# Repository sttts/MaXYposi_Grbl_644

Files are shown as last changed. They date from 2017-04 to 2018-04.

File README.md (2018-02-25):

GitHub Logo

Maker Media GmbH und c't, Heise Zeitschriften Verlag

***

### MaXYposi-Schrittmotorsteuerung 

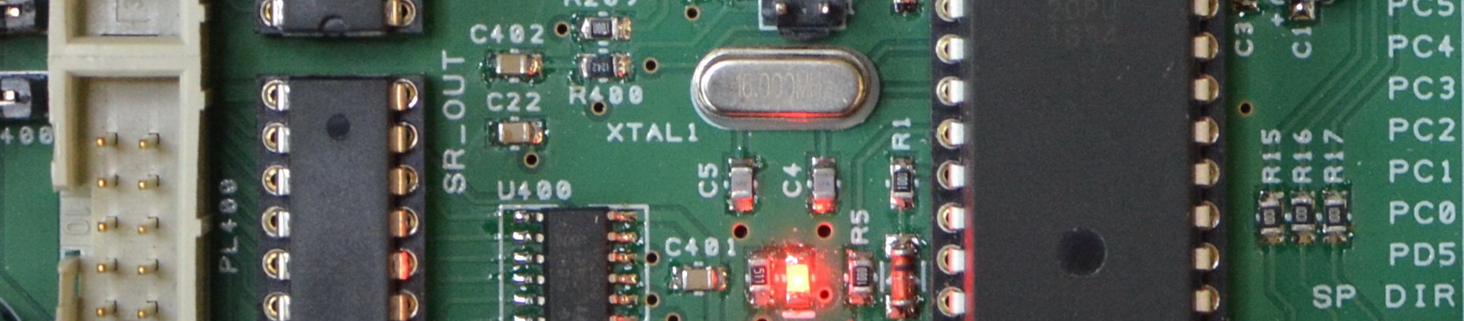
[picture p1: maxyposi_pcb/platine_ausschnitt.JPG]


Unser auf GRBL basierendes CNC-Steuerungs-Projekt für **4 Achsen und vielen 
I/Os** auf einer speziell für CNC-Zwecke ausgelegten Platine. Natürlich wäre als 
Bahnsteuerung auch ein normaler Arduino-328 mit dem Standard-GRBL geeignet - wir 
haben unser GRBL-644 allerdings auf 4 Achsen erweitert und 32 I/Os hinzugefügt, 
außerdem einen Handrad- und Joystick-Jog-Anschluss sowie eine Echtzeit-
Positionsanzeige mit LCD 16x2 auf einem (optionalen) Bedienfeld. 

Die mit allen SMD-Bauteilen vorbestückte Platine wird mit einem programmierten 
ATmega644A (Optiboot-Bootloader und GRBL 1.1f4 ohne Kontrollpult-Unterstützung) geliefert und kann 
im [Heise Shop](https://shop.heise.de/sonstiges/make-projekte/maxyposi) bestellt werden. Weitere Hinweise
finden Sie auf der [MaXYPosi-Projektseite](http://www.make-magazin.de/maxyposi). 

**Wichtig:** Für den Einsatz des MaXYpulti-Kontrollpults müssen Sie den Arduino-Sketch neu kompilieren und hochladen 
(Hinweise dazu im Unterverzeichnis **[MaXYpulti PCB](https://github.com/heise/MaXYposi_Grbl_644/tree/master/maxypulti_pcb)**).

Dokumentationen zu verschiedenen Treiberkarten finden Sie im **[TB6560-BOARDS-Repository](https://github.com/heise/TB6560-BOARDS)**. 

Bitte beachten Sie unbedingt: 

* den Artikel in **[Make: 2/2017](https://shop.heise.de/katalog/make-2-2017)**
* unsere **[MaXYPosi-Projektseite](http://www.make-magazin.de/maxyposi)**
* die ständig aktualisierte **[FAQ-Seite](https://heise.de/-3676050)** und das zugehörige Forum.
* die Hinweise zur Bestückung der Steuerungsplatine **[im Unterverzeichnis MaXYposy PCB](https://github.com/heise/MaXYposi_Grbl_644/tree/master/maxyposi_pcb)**
* die Hinweise zur Bestückung der Kontrollpult-Platine **[im Unterverzeichnis MaXYpulti PCB](https://github.com/heise/MaXYposi_Grbl_644/tree/master/maxypulti_pcb)**
* das Programm für den Kontrollpult-Display-Prozessor **[im Unterverzeichnis GRBL Display](https://github.com/heise/MaXYposi_Grbl_644/tree/master/grbl_display)**

Optional:

* Sketch SD-Card-Sender für Arduino Uno/Nano **[im Unterverzeichnis SDcard Sender](https://github.com/heise/MaXYposi_Grbl_644/tree/master/sdcard_sender)**
* Alter Schrittmotor als Dreh-Encoder/Handrad **[im Unterverzeichnis Step Encoder](https://github.com/heise/MaXYposi_Grbl_644/tree/master/step_encoder)**

Der Sketch "grblUpload_644.ino" kompiliert GRBL-644 und lädt ihn auf die MaXYposi-Platine. Bitte 
richten Sie die Arduino-IDE folgendermaßen ein:

* Laden Sie sich das [GRBL-644-Repository](https://github.com/heise/MaXYposi_Grbl_644/archive/master.zip) herunter und entpacken sie es auf der lokalen Festplatte.
* Verschieben Sie das Verzeichnis "grblUpload_644" vom Github-Download in Ihren "Arduino"-Sketch-Ordner.
* Verschieben Sie das Verzeichnis "hardware" vom Github-Download in Ihren "Arduino"-Sketch-Ordner.
* Verschieben Sie das Verzeichnis "libraries\grbl_644" vom Github-Download nach "Arduino\libraries\grbl_644".
* Öffnen Sie den Sketch "..\Arduino\grblUpload_644\grblUpload_644.ino"
* Wählen Sie im Menü "Werkzeuge:Board" den Eintrag "MaXYposi".
* Wählen Sie im Menü "Werkzeuge:Prozessor" den Eintrag "ATmega644A" oder "ATmega644P", je nachdem, welche Variante Sie verwenden.

Sie können nun GRBL mit der Arduino-IDE kompilieren und auch auf das Board 
hochladen; die mit der Platine gelieferten Prozessoren sind bereits mit einem 
Sanguino-Optiboot-kompatiblen Bootloader ausgestattet. Die hier verfügbaren HEX-
Dateien sind für einen ATmega644A (für den ausgelieferten Bausatz) kompiliert.

### Version history

### Grbl 1.1f5 Version for ATmega644(p) build 02/24/2018 (english)

 * Fixed issue with $I (GRBL info command; additional info separated with ":"), build date format now VERSION.MM/DD/YYYY
 * Fixed "Jog crash after G38.2 Probing" bug
 * Fixed "M104..M107 not accepted while running" bug (build 02/24/2018)
 * MaXYpulti control panel defined in **config.h** by default

### Grbl 1.1f4 Version for ATmega644(p) build 05.11.2017 (english)

 * Fixed compile errors when C axis disabled
 * Fixed erraneous behaviour when M100 to M107 commands are used
 
### Grbl 1.1f3 Version for ATmega644(p) build 20.06.2017 (english)

 * Fixed pin assignment for SR inputs (joystick)
 * Laser Mode disables Z homing (prevents alarm if no Z axis limit switch connected)

### Grbl 1.1f2 Version for ATmega644(p) build 18.03.2017 (english)

GRBL firmware with multiple additions, suited for MaXYposi board (german Make: magazine, issue 2/2017). Additions by Carsten Meyer, Make Magazin Deutschland.

* 4th C axis per #define in config.h, settings configured to C360 = 1 complete turn for PNP machine or robot head @ 1/16 steps driver
* 16 Output ports for LEDs and relays, via HC595 SRs on SPI (may left unconnected)
* 32 Input ports for buttons/swiches, via HC165 SRs on SPI (may left unconnected)
* SPI transfer of realtime position data (floats), for external LCD (needs extra ATmega168/328)
* Support for dial/handwheel, direct connection to Grbl CPU. Updates machine/work position in realtime.
* Support for analog joystick with variable speed, direct connection to Grbl CPU. Updates machine/work position in realtime.
* Handwheel A/B phase on 2 port pins, must be same as LIMIT port
* Joystick on SR inputs, speed on ADC7
* Optional button panel with coordinate LCD 16x2 and up to 32 buttons, connected via SPI
* Button functions and enables defined in cpu_map.h
* M commands for additional relay switches M100/101..M106/M107 (even numbers turn on, odd turn off relays)
* Additional $I fields and build info
* New files: spi_sr.c and jogpad.c to handle SPI Rx/Tx and joystick/buttons/dial
* some additions to other filed to handle 4th axis and display/LED update

Please note ATmega644 output pin onfiguration in cpu_map.h, which heavily differs from Arduino pinout.

Put in your Arduino Sketchbook folder and select board "MaXYposi" and CPU ATmega644 or 644p.

WORK IN PROGRESS. STAY TUNED.

Grbl Logo

* [Licensing](https://github.com/gnea/grbl/wiki/Licensing): Grbl is free software, released under the GPLv3 license.
* For more information and help, check the Grbl **[Wiki pages!](https://github.com/gnea/grbl/wiki)**!
* Lead Developer: Sungeun "Sonny" Jeon, Ph.D. (USA) aka @chamnit
* Built on the wonderful Grbl v0.6 (2011) firmware written by Simen Svale Skogsrud (Norway).

-------------
Grbl is an open-source project and fueled by the free-time of our intrepid administrators and altruistic users. If you'd like to donate, all proceeds will be used to help fund supporting hardware and testing equipment. Thank you!



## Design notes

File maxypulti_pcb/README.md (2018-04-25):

GitHub Logo

Maker Media GmbH und c't, Heise Zeitschriften Verlag

***

### MaXYposi-Schrittmotorsteuerung, Stückliste Kontrollpult

In diesem Unterverzeichnis finden Sie die Stücklisten, Schalt- und Bestückungspläne 
zur MaXYposi-Schrittmotorsteuerung, Kontrollpult (MaXYpulti).

    Bauteil                                   Anzahl Name/Bemerkung
    =============================================================================
    
    PSS 254/4G, Wire-To-Board 4-pol. RM2,54      1   PL6
    PSS 254/5G, Wire-To-Board 4-pol. RM2,54      2   PL1 PL2
    PSS 254/6G, Wire-To-Board 4-pol. RM2,54      2   PL1 PL4    
    Zweireihige Pfostenleiste RM 2.54            1   PL3                 
    WSL 16, Wannenstecker 16pol.                 1   PL5               
    Jumper 2pol. RM2.54                          1   JP1                 
    14WP, Zweireihige Pfostenleiste RM 2.54      1   PL7 (siehe Text unten)                

    74HC165 DIL                                  4   U4 U5 U6 U7         
    74HC595 DIL                                  2   U8 U9               
    ATmega328-DIL                                1   U3  (ggf. mit Bootloader)               
    DS26LS32CM DIL                               1   U1  (oder AM26LS32ACN)                
    22p RM5                                      2   C3 C5               
    100n RM5                                     8   C6 C4 C1 C10 C11 C12 C13 C14           
    10µ 63V                                      4   C7 C9  C2 C8              
    LCD alphanum 2x16 Zeichen                    1   U2                  
    LED rot 3mm                                  1   LED1                
    4k7                                          1   R6                  
    10k                                          1   R2                  
    10R                                          1   R3                  
    220R                                         3   R7 R8 R9            
    1K                                          16   R15 R20 R21 R22 R23 R24 R25 R26 R27 R28 R29 R30 R31 R32 R33 R34
    4k7                                          1   R19                 
    22k                                          1   R4                  
    100R                                         8   R12 R10 R11 R13 R14 R16 R17 R18
    SIL 9-8 10k Netzwerk 8-fach, 9-pin           4   RN3 RN4 RN5 RN6     
    Print-Poti Alps, RK11K113-LOG10K             1   P1  (auch RK11K113-LIN10K oder 50K möglich)     
    Trimmer 5mm, 2k5                             1   R1                  
    Taster Multimec 3FTH9                       30   SW1..SW34
    Taster Multimec 3ATH9                        4   SW3, SW6, SW8, SW9   
    Quartz 16 MHz HC49U                          1   XTAL1 

    =============================================================================

Beachten Sie die Hinweise im Artikel zu den LED-Vorwiderständen. Diese sind hier 
pauschal mit 1k für blaue/weiße LEDs angegeben, müssen aber für eine ungefähr 
gleiche Helligkeit der einzelnen Farben angepasst werden. Der jeweilige 
Vorwiderstand ist immer in der Nähe des zugehörige Tasters.

PL7 kann alternativ für ein Display mit seitlichem 14pol. Anschluss verwendet 
werden und wird bei 16x2-Standard-Displays nicht benötigt. Hierfür sollten Sie 
eine einreihige Pfostenleiste RM 2,54 mm mitbestellen.

Die LEDs für die Taster sowie die Tastenkappen sind in der Stückliste NICHT 
aufgeführt. Wählen Sie die Farben nach persönlichem Gusto. Wir haben die Farben 
wie folgt gewählt: Blau = X (Kappe 1D00), Grün = Y (Kappe 1D02), Rot = Z (Kappe 
1D08), Gelb = C-Achse (Kappe 1D04). Die transparent-weißen Tastenkappen haben 
die Bezeichnung 1D16, die schwarzen heißen 1D09. beachten Sie zur Auswahl der 
Farben auch die Bilder im Artikel.

[Flachkopf-LEDs von LED1.de](https://www.led1.de/shop/standard-leds/led-3mm-ultrahell-flat-top/)

[Tastenkappen Serie 1Dxx von MEC Switches, Beispielfarbe Rot, bei Reichelt](https://www.reichelt.de/Kurzhubtaster/KAPPE-1D08/3/index.html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)

[Tastenkappe Serie 1ZCxx von MEC Switches, Jogpad-Mittelkreis, Beispielfarbe Schwarz, bei Reichelt](https://www.reichelt.de/Kurzhubtaster/KAPPE-1ZC09/3/index.html?ACTION=3&LA=2&ARTICLE=79739)

[Tastenkappen Serie 1ZBxx von MEC Switches, Jogpad-Außenkreis, Beispielfarbe Schwarz, bei Reichelt](https://www.reichelt.de/Kurzhubtaster/KAPPE-1ZB09/3/index.html?ACTION=3&LA=517&ARTICLE=79744)

Bitte denken Sie bei einer Bestellung auch an Zubehör wie Flachbandkabel, Steck-
und Pfostenverbinder.

Wer unbestückte Platinen fertigen (lassen) will, kann die Gerber- und 
Bohrdateien "maxypulti_gerber.zip" herunterladen. Bitte beachten Sie: Das Layout 
unterliegt unserem Copyright und darf **nur für private Zwecke** verwendet 
werden. Für eine kommerzielle Nutzung [kontaktieren Sie bitte die 
Redaktion](https://www.heise.de/make/kontakt/).

Vorlagen für die Frontplatte liegen in zwei Versionen vor: Mit und ohne 
Ausschnitt für ein CNC-Handrad (Dial), jeweils als DXF-, SVG- und CorelDraw-Datei. 
Die Vorlagen eignen sich zum Plexiglas-Zuschnitt mit Beschriftung bei einem 
Dienstleister Ihrer Wahl, z.B. www.formulor.de oder einem beliebigen Fablab mit 
Lasercutter.

#### AVR-CPU für Display

Als Prozessor empfehlen wir einen ATmega328p mit bereits installiertem 
Bootloader, erhältlich zum Beispiel bei [Watterott 
electronic](http://www.watterott.com/de/ATmega328-Arduino-Bootloader); damit ist 
das Flashen der GRBL-Display-Firmware über die Arduino-IDE möglich: Geben Sie 
als Board den Arduino Nano an und verwenden Sie einen USB-Seriell-Wandler mit 
FTDI-Chip. Ansonsten benötigen Sie zum Flashen
[einen ISP-Programmer](https://www.reichelt.de/Programmer-Entwicklungstools/DIAMEX-PROG-S2/3/index.html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). 
Beachten Sie auch die Leser-Anleitung unten auf dieser Seite.

#### GRBL-644 anpassen

Um das MaXYposi-GRBL mit unserem Kontrollpult einzusetzen, müssen Sie in der 
Datei **config.h** die Zeilen
```
#define USER_PANEL_SMALL 
// #define USER_PANEL_LARGE 
```
ändern in
```
// #define USER_PANEL_SMALL 
#define USER_PANEL_LARGE 
```
und den Sketch **grblUpload_644.ino** neu kompilieren.

#### Weitere Tipps

Unser Leser **[HorstBaerbel](https://github.com/HorstBaerbel)** hat 
dankenswerterweise das Programmieren des HEX-Files für den Display-Prozessor 
genauer beschrieben - im Heft wurde die Prozedur nur kurz angerissen. Außerdem 
hat er hier einige wichtige Hinweise zusammengetragen. Vielen Dank dafür! :+1: 

* Das Label für C9 fehlt auf dem Bestückungsdruck.

* Bei allen anderen Tastern ist es egal, aber die vier speziellen Taster (Multimec 3ATH9) für das Jogpad MÜSSEN in der richtigen Orientierung eingebaut werden (grob umschrieben "Verriegellungsnasen innen")! Der "Strich" auf dem Bestückungsplan ist etwas irreführend da die MEC-Taster sowohl eine Kante, als auch einen solchen Strich haben. Ein Hinweis wäre praktisch, auslöten nervt nämlich ;)

* Ich habe für P1 das Poti "RK11K113-LOG10K" von Reichelt bestellt. Leider ist die Achse etwas kurz, so dass ev. "RK09K113-LOG10K" besser wäre. Dort müsste man dann allerdings die Achse kürzen. Man kann das "RK11K113-LOG10K" aber auch, wie die Joypad-Taster, mit 1,5mm Abstand zur Platine einbauen um möglichst viel von der Achse zum klemmen übrig zu haben.

* Der "DS26LS32CM" ist bei Reichelt nicht zu bekommen, aber der Ersatztyp "AM26LS32ACN".

* Der "74LS595" ist bei Reichelt nicht zu bekommen, als Ersatz aber der "74HC595".

* Die Teilenummer des 16MHz-Quartzes ist "16,0000-HC49U-S".

* Der Drehencoder / Handrad ist z.B. bei Ebay sehr gut mit der Suche "100PPR hand wheel" zu finden.

* Wer die lange Versandzeit nicht scheut bekommt einen ganzen Satz 
verschiedenfarbige straw-hat-LEDs z.B. von Aliexpress. Man findet mit der Suche 
"flat top led mix" einige Angebote für 5*20 LEDs (RGBYW) um die 3€...

* Die Firmware mit einem Arduino als ISP auf den ATMEGA328P zu bringen ist nicht ganz einfach. Hier meine Anleitung (für Linux, sollte aber auch für andere OS gehen):

  *  Nach dem Tutorial [hier](https://www.arduino.cc/en/Tutorial/ArduinoISP) den Arduino mit einem ISP-Sketch versehen und mit dem MaxyPulti verbinden. Im Detail bei einem Arduino UNO oder Pro als ISP: (Arduino ISP->MaxyPulti PL3) ISP1->9, ISP2->2, ISP3->7, ISP4->1, ISP5->4 und Arduino Pin 10->5.

  * In den Arduino-IDE-Voreinstellungen "Ausführliche Ausgabe während ... Hochladen" aktivieren.

  * Als Board "Arduino/Genuino UNO" und als Programmer "Arduino as ISP" einstellen und auf "Bootloader brennen" klicken. Nun sollte der Bootloader installiert sein.

  * Die erste Kommandozeile aus dem Ausgabefenster kopieren (fett markierter Teil). Sie sollte in etwa so aussehen: "**/home/USERNAME/.arduino15/packages/arduino/tools/avrdude/6.3.0-arduino9/bin/avrdude -C/home/USERNAME/.arduino15/packages/arduino/tools/avrdude/6.3.0-arduino9/etc/avrdude.conf -v -patmega328p -cstk500v1 -P/dev/ttyACM0 -b19200 -Uflash:w:**/home/USERNAME/.arduino15/packages/arduino/hardware/avr/1.6.21/bootloaders/optiboot/optiboot_atmega328.hex:i -Ulock:w:0x0F:m". Hier ist USERNAME der Name des angemeldeten Benutzers.

  * Die Datei "grbl_display.hex" herunterladen. Terminal öffnen und in das Verzeichnis mit der Datei wechseln.

  * Kommandozeile für HEX-Upload zusammenbauen (oben kopierter Teil, plus fett markierter Teil): "/home/USERNAME/.arduino15/packages/arduino/tools/avrdude/6.3.0-arduino9/bin/avrdude -C/home/USERNAME/.arduino15/packages/arduino/tools/avrdude/6.3.0-arduino9/etc/avrdude.conf -v -patmega328p -cstk500v1 -P/dev/ttyACM0 -b19200 -Uflash:w:**grbl_display.hex -D**".

  * Nachdem der Upload fertig ist, sollte LED1 auf dem MaxyPulti rhythmisch blinken.

* In der Frontplatte ist das Loch für P1 mmn zu groß; 7mm sollten laut Schieblehre für den "RK11K113-LOG10K" reichen.

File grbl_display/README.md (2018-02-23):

GitHub Logo

Maker Media GmbH und c't, Heise Zeitschriften Verlag

***

### MaXYposi-Schrittmotorsteuerung, Programm für Display-ATmega328p

Das Programm existiert derzeit nur für den Compiler AVRco Pascal von e-Lab.de (kostenlos für ATmega8/88 und alle Programme unter 4 kByte). Ein Port auf Arduino ist in Arbeit.

Das hiermit erstellte Hex-File grbl_display.hex lässt sich trotzdem problemlos mit der Arduino-IDE auf einen ATmega328p mit bereits geflashtem Bootloader (z.B. von Watterott oder Adafruit) überspielen.

#### GRBL-644 anpassen

Um das MaXYposi-GRBL mit unserem Kontrollpult einzusetzen, müssen Sie in der 
Datei **config.h** die Zeilen
```
#define USER_PANEL_SMALL 
// #define USER_PANEL_LARGE 
```
ändern in
```
// #define USER_PANEL_SMALL 
#define USER_PANEL_LARGE 
```
und den Sketch **grblUpload_644.ino** neu kompilieren.

#### Weitere Tipps

Unser Leser **[HorstBaerbel](https://github.com/HorstBaerbel)** hat dankenswerterweisedas 
Programmieren des HEX-Files für den Display-Prozessor genauer beschrieben - im 
Heft wurde die Prozedur nur kurz angerissen. Vielen Dank dafür! :+1: 

* Die Firmware mit einem Arduino als ISP auf den ATMEGA328P zu bringen ist nicht ganz einfach. Hier meine Anleitung (für Linux, sollte aber auch für andere OS gehen):

*  Nach dem Tutorial hier den Arduino mit einem ISP-Sketch versehen und mit dem MaxyPulti verbinden. Im Detail bei einem Arduino UNO oder Pro als ISP: (Arduino ISP->MaxyPulti PL3) ISP1->9, ISP2->2, ISP3->7, ISP4->1, ISP5->4 und Arduino Pin 10->5.

* In den Arduino-IDE-Voreinstellungen "Ausführliche Ausgabe während ... Hochladen" aktivieren.

* Als Board "Arduino/Genuino UNO" und als Programmer "Arduino as ISP" einstellen und auf "Bootloader brennen" klicken. Nun sollte der Bootloader installiert sein.

* Die erste Kommandozeile aus dem Ausgabefenster kopieren (fett markierter Teil). Sie sollte in etwa so aussehen: "/home/USERNAME/.arduino15/packages/arduino/tools/avrdude/6.3.0-arduino9/bin/avrdude -C/home/USERNAME/.arduino15/packages/arduino/tools/avrdude/6.3.0-arduino9/etc/avrdude.conf -v -patmega328p -cstk500v1 -P/dev/ttyACM0 -b19200 -Uflash:w:/home/USERNAME/.arduino15/packages/arduino/hardware/avr/1.6.21/bootloaders/optiboot/optiboot_atmega328.hex:i -Ulock:w:0x0F:m". Hier ist USERNAME der Name des angemeldeten Benutzers.

* Die Datei "grbl_display.hex" herunterladen. Terminal öffnen und in das Verzeichnis mit der Datei wechseln.

* Kommandozeile für HEX-Upload zusammenbauen (oben kopierter Teil, plus fett markierter Teil): "/home/USERNAME/.arduino15/packages/arduino/tools/avrdude/6.3.0-arduino9/bin/avrdude -C/home/USERNAME/.arduino15/packages/arduino/tools/avrdude/6.3.0-arduino9/etc/avrdude.conf -v -patmega328p -cstk500v1 -P/dev/ttyACM0 -b19200 -Uflash:w:grbl_display.hex -D".

* Nachdem der Upload fertig ist, sollte LED1 auf dem MaxyPulti rhythmisch blinken.

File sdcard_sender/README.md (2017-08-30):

GitHub Logo

Maker Media GmbH und c't, Heise Zeitschriften Verlag

***

### MaXYposi-Schrittmotorsteuerung, SD-Card-Sender

Simpler Arduino-Sketch zum Senden von G-Code-Files an MaXYposi-GRBL. Läuft auf einem Standard-Arduino mit SD-Card-Shield, der als separater Zuspieler dient. Nur zur Demo gedacht, hat sicher noch Bugs und ist nur ein Quick&Dirty-Versuch.

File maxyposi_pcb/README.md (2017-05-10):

GitHub Logo

Maker Media GmbH und c't, Heise Zeitschriften Verlag

***

### MaXYposi-Schrittmotorsteuerung, Stückliste Mainboard

In diesem Unterverzeichnis finden Sie die Stücklisten, Fotos, Schalt- und Bestückungspläne 
zur MaXYposi-Schrittmotorsteuerung, Mainboard.

Die mit allen SMD-Bauteilen vorbestückte Platine wird mit einem programmierten 
ATmega644A (Optiboot-Bootloader und GRBL 1.1f2) ausgeliefert. Es sind noch 
einige bedrahtete Bauteile zu beschaffen und zu bestücken, unter anderem die 
Steckverbinder und IC-Fassungen. Wir haben hier die Reichelt-Bestellnummern 
angegeben:

    Bauteil                               Anzahl Name/Bemerkung
    =============================================================================
    Jumper-Pfostenleiste 2-pol.              6   JP300 JP400 JP401 JP1 JP2 JP3
    Jumper-Pfostenleiste 3-pol.              1   JP5 
    Pfostenleisten einreihig                 1   PL5, PL15, PL16 (falls benötigt) 
    (für diese Positionen SL 1x50G 2,54 bestellen und auf Länge kürzen)       
    
    PSS 254/2G, Wire-To-Board 2-pol. RM2,54  2   PL7 PL9             
    PSS 254/3G, Wire-To-Board 3-pol. RM2,54  1   PL4                 
    PSS 254/4G, Wire-To-Board 4-pol. RM2,54  6   PL201 PL202 PL203 PL6 PL204 PL8
    PSS 254/5G, Wire-To-Board 5-pol. RM2,54  2   PL16 PL10           
    PSS 254/6G, Wire-To-Board 6-pol. RM2,54  2   PL3 PL2             
    WSL 10, Wannenstecker                    5   PL1 PL400 PL401 PL301 PL300
    WSL 16, Wannenstecker                    1   PL501               
    FL-B 64G4, Federleiste A-B DIN41612      2   CON1 CON2 (falls benötigt)
    RND 205-00179, Steckv. 4pol.             1   SV Stromversorgung    
    RND 205-00201, Stiftleiste 90°           1   SV Stromversorgung    
    220µ 63V RM5                             1   C18                 
    D-SUB BU 25US, D-Sub 25-pol. Female      1   CON5               
    LM 317 TO92                              1   U500                
    (ATmega644A-PU, DIL)                     1   U1 (mitgeliefert!)                 
    SIL 9-8 10K, R-Netzw. 8x 10k             2   RN300 RN301         
    ULN 2803A (DIL)                          2   U402 U403           
    16,0000-HC49U-S, Quarz 16 MHz HC49U      1   XTAL1               
    GS 40P, IC-Fassung 40pol DIL             1
    GS 18P, IC-Fassung 18pol DIL             2

Bitte denken Sie bei einer Bestellung auch an Zubehör wie Flachbandkabel, Steck-
und Pfostenverbinder.

Wer unbestückte Platinen fertigen (lassen) will, kann die Gerber- und 
Bohrdateien "grbl_maxyposi_gerber.zip" herunterladen. Bitte beachten Sie: Das 
Layout unterliegt unserem Copyright und darf **nur für private Zwecke** verwendet 
werden. Für eine kommerzielle Nutzung [kontaktieren Sie bitte die 
Redaktion](https://www.heise.de/make/kontakt/).

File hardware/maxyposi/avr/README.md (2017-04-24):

#### MaXYposi Bootloader

Derived from **Sanguino by Kristian Sloth Lauszus, 2012**, MaXYposi additions by -cm

Nur für "jungfräuliche" Controller ohne installierten Bootloader!

Falls noch nicht vorhanden, kann mit einem ISP-Programmer (oder einem dazu umfunktionierten Arduino) dieser Bootloader auf den MaXYposi-Controller ATmega644P geflasht werden. Die Befehlszeilen für avrdude lauten etwa wie folgt (beachten Sie die Fuses-Settings):

avrdude.exe -C "avrdude.conf" -pm644p -cstk500v2 -B8 -P COM%1 -V -s -U lfuse:w:0xFF:m -U hfuse:w:0xDE:m -U efuse:w:0xFC:m -U lock:w:0xEF:m

avrdude.exe -C "avrdude.conf" -pm644p -cstk500v2 -B2 -P COM%1 -U flash:w:"optiboot_atmega644p.hex":i

_________

The code is released under the GNU General Public License.

This content is needed so it's compatible with the Arduino IDE 1.5.x.

For more information see the following sites: [http://www.arduino.cc/en/Guide/Environment#thirdpartyhardware](http://www.arduino.cc/en/Guide/Environment#thirdpartyhardware) and [http://code.google.com/p/arduino/wiki/Platforms1](http://code.google.com/p/arduino/wiki/Platforms1)
or send me an email at <a href="mailto:lauszus@gmail.com?Subject=Sanguino">lauszus@gmail.com</a>.

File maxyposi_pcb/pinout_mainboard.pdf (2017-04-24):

Endstufenanschluss (LPT, D-Sub 25)
Pin | Funktion | Beschreibung
1 | ENA | Schrittmotoren einschalten
2 | X PULSE | Schrittimpuls X
3 | X DIR | Drehrichtung X
4 | Y PULSE | Schrittimpuls Y
5 | Y DIR | Drehrichtung Y
6 | Z PULSE | Schrittimpuls Z
7 | Z DIR | Drehrichtung Z
8 | C PULSE | Schrittimpuls C (optional)
9 | C DIR | Drehrichtung C
10 | SW X LIMIT | Endschalter X-Achse, linker Anschlag
11 | SW Y LIMIT | Endschalter Y-Achse, vorderer Anschlag
12 | SW Z LIMIT | Endschalter Z-Achse, oberer Anschlag
13 | SW PROBE | Werkzeuglängen-Sensor (optional)
14 | REL SPINDLE | Spindelmotor-Relais oder PWM
15..17 | NC | (nicht benutzt)
18..25 | Masse, 0V

PL300: Nullpunkte/Homing
Pin | Funktion | Beschreibung
1 | ZERO X | Werkstück-Nullpunkt X auf aktuelle Position setzen
2 | ZERO Y | Werkstück-Nullpunkt Y auf aktuelle Position setzen
3 | ZERO Z | Werkstück-Nullpunkt Z auf aktuelle Position setzen
4 | ZERO C | Nullpunkt C-Achse auf aktuelle Position setzen
5 | FEED PLUS | Override für Vorschub, schneller
6 | FEED MINUS | Override für Vorschub, langsamer
7 | CLEAR ALARM Alarm ausschalten, z.B. bei misslungenem Homing -- Vorsicht!
8 | HOMING | Maschinen-Nullfahrt an die Endschalter durchführen
9 | VCC | Versorgungsspannung (hier unbenutzt)
10 | GND | Masse, gemeinsamer Pol für alle Taster

PL301: Joystick-Anschluss
Pin | Funktion | Beschreibung
1 | JOY_FWD_X | Jog mit Joystick in positiver X-Richtung
2 | JOY_REV_X | Jog mit Joystick in negativer X-Richtung
3 | JOY_FWD_X | Jog mit Joystick in positiver Y-Richtung
4 | JOY_REV_X | Jog mit Joystick in negativer Y-Richtung
5 | JOY_FWD_X | Jog mit Joystick in positiver Z-Richtung
6 | JOY_REV_X | Jog mit Joystick in negativer Z-Richtung
7 | JOY_FWD_X | Jog mit Joystick C im Uhrzeigersinn
8 | JOY_REV_X | Jog mit Joystick C entgegen Uhrzeigersinn
9 | VCC | Versorgungsspannung (hier unbenutzt)
10 | GND | Masse

PL400: Zubehör-Relais
Pin | Funktion | Beschreibung
1 | SPINDLE_ENA | Spindelmotor-Relais und/oder Kontroll-LED, Minuspol
2 | SPINDLE_DIR | Spindelmotor-Drehrichtungs-Relais und/oder Kontroll-LED (optional) , Minuspol
3 | FLOOD | M8 Kühlmittel-Relais/Ventil (optional), wird mit M9 ausgeschaltet, Minuspol
4 | MIST | M7 Nebelkühlung-Relais/Ventil (optional), wird mit M9 ausgeschaltet, Minuspol
5 | ATC | Werkzeugwechsler-Relais (Ein mit M100, Aus mit M101) , Minuspol
6 | AUX1 | Zubehör-Relais/Ventil (Ein mit M102, Aus mit M103) , Minuspol
7 | AUX2 | Zubehör-Relais/Ventil (Ein mit M104, Aus mit M105) , Minuspol
8 | AUX3 | Zubehör-Relais/Ventil (Ein mit M106, Aus mit M107) , Minuspol
9 | VCC_REL | Versorgungsspannung Relais (bis 24V)
10 | GND | Masse.

Die Endschalter-Eingänge 10 bis 13 sind parallel zu den LIMIT-Eingängen PL2 geschaltet und können alternativ zu diesen benutzt werden.

Die Jog-Geschwindigkeit wird mit einem Potentiometer an PL10 eingestellt. Alle Joystick-Taster (oder Mikroschalter in Industrie-Joysticks) schalten nach Masse.

Die Ausgangstreiber schalten ihre Last nach Masse (gemeinsamer Pluspol). Relais etc. müssen mit einer eigenen Spannung versorgt werden, falls mehr als 5V benötigt werden; diese ist dann zusätzlich an Pin 9 zuzuführen (JP 400 offen!). Bei 5V-Relais/Verbrauchern wird Jumper JP400 gesteckt.

PL401: Maschinenstatus
Pin | Funktion | Beschreibung
1 | LED_ALARM | LED blinkt im Alarm-Fall (Maschine ohne Nullfahrt, Reset im Betrieb), Minuspol (Kathode)
2 | LED_RUN | LED leuchtet, während Schrittmotoren laufen (auch bei Jog und Homing), Minuspol (Kathode)
3 | LED_HOLD | LED blinkt, wenn HOLD-Taster gedrückt wurde, Minuspol (Kathode)
4 | DIAL_FAST | (optionales) Handrad im Grob-Modus (10mm pro Umdrehung)
5 | DIAL_X | (optionales) Handrad steuert X-Achse
6 | DIAL_Y | (optionales) Handrad steuert Y-Achse
7 | DIAL_Z | (optionales) Handrad steuert Z-Achse
8 | DIAL_C | (optionales) Handrad steuert C-Achse
9 | VCC_REL | Versorgungsspannung LEDs/Relais (bis 24V)
10 | GND | Masse.

PL7: Hardware-Reset
Pin | Funktion | Beschreibung
1 | GND | Masse
2 | HW_RESET | Hardware-Reset, Maschine stoppt sofort (Not-Ausschalter)

PL8: Maschinensteuerung
Pin | Funktion | Beschreibung
1 | GND | Masse
2 | SW_RESET | Soft-Reset, Maschine stoppt sofort
3 | SW_HOLD | Anhalten und warten. HOLD-LED blinkt im Wartemodus
4 | SW_START | Ausführung fortsetzen, falls HOLD aktiv war.

PL3: Serial I/O
Pin | Funktion | Beschreibung
1 | GND | Masse
2, 6 | CTS_RESET | Reset für Aufruf des Bootloaders, Arduino-kompatibel
3 | VCC | +5V vom USB-Seriell-Wandler, über JP3 mit 5V-Versorgungsspannung verbunden
4 | RxD | Empfangsdaten vom USB-Seriell-Wandler TxD-Anschluss
5 | TxD | Sendedaten zum USB-Seriell-Wandler RxD-Anschluss

PL4: Werkzeuglängen-Sensor
Pin | Funktion | Beschreibung
1 | GND | Masse
2 | PROBE | (optionaler) Werkzeuglängen-Sensor, schaltet nach Masse wenn aktiv
3 | VCC_PRB | Versorgungsspannung für Werkzeuglängen-Sensor oder dessen Kontroll-LED

PL10: Handrad-Anschluss
Pin | Funktion | Beschreibung
1 | GND | Masse, linker Poti-Anschluss
2 | ENC_0 | Phase 0 oder A des (optionalen) Handrades
3 | ENC_1 | Phase 1 oder B des (optionalen) Handrades
3 | ANALOG | Schleifer des Jog-Geschwindigkeits-Potis, mittlerer Anschluss
5 | VCC_ENC | +5V-Versorgungsspannung für Handrad, rechter Poti-Anschluss

CON1 bis 4: DIN-Steckleisten
Pin | Port | Funktion
1 | PB0 | SW_RESET
2 | PB1 | SW_HOLD
3 | PB2 | SW_START
4 | PB3 | Slave Select Ausgangs-Schieberegister
5 | PB4 | Slave Select Display und Eingangs-Schieberegister

Die Versorgungsspannung des Werkzeuglängen-Sensors kann mit JP entweder auf 5V oder die Motor-Betriebsspannung V36 (12 bis 36V) gelegt werden. Viele beleuchtete Taster benötigen 24V für die Kontroll-LED.

Sollte das Handrad in die falsche Richtung steuern, sind ENC_0 und ENC_1 zu vertauschen. Das Handrad muss in den GRBL-Sourcen freigeschaltet sein, die Auswahl der Achse geschieht dann über PL301 und wird mit den LEDs an PL401 angezeigt. Der Anschluss am linken Poti-Anschlag kommt an Masse, der rechte an +5V (VCC_ENC). Der Widerstandswert des Potis ist unkritisch, er sollte zwischen 5 und 50 kOhm betragen.

Die Ausgangstreiber schalten ihre Last nach Masse (gemeinsamer Pluspol). Für Anzeige-LEDs mit 5V Betriebsspannung (Vorwiderstand 220 bis 470 Ohm nicht vergessen!) ist JP401 zu stecken, die gemeinsame Anode kommt dann an Pin 9.

6 | PB5 | MOSI | Serielle Daten an Display oder Ausgangs-
7 | PB6 | MISO | Serielle Daten von Eingangs-Schieberegistern
8 | PB7 | SCK | Takt für SPI
9 | GND | Masse
10 | VCC | +5V
11 | GND | Masse
12 | SHIFT_IN | Serielle Daten an Eingangs-Schieberegister (für Kaskadierung)
13 | PA0 | X_LIMIT, X-Endschalter
14 | PA1 | Y_LIMIT, Y-Endschalter
15 | PA2 | Z_LIMIT, Z-Endschalter
16 | PA3 | PROBE, Längensensor-Eingang
17 | PA4 | C_LIMIT, C-Endschalter
18 | PA5 | ENC_0, Quadratur-Phase 0/A Handrad
19 | PA6 | ENC_1, Quadratur-Phase 1/B Handrad
20 | PA7 | Analog-Eingang Joystick-Geschwindigkeit, 0 bis 5V
21 | PC7 | C_DIR, Drehrichtung C-Motor
22 | PC6 | C_STEP, Schrittimpuls C-Motor
23 | PC5 | Z_DIR
24 | PC4 | Z_STEP
25 | PC3 | Y_DIR
26 | PC2 | Y_STEP
27 | PC1 | X_DIR
28 | PC0 | X_STEP
29 | PD5 | STEP_ENA, Schrittmotoren einschalten
30 | PD6 | SPINDLE_DIR, Drehrichtung Frässpindel
31 | PD7 | SPINDLE_PWM, pulsbreitenmoduliertes Signal für Spindel-Drehzahl
32 | V36 | Motor-Betriebsspannung für kleine Endstufen

PL201, 202 und 203: Ausgänge für Einzel-Endstufen
Pin | Funktion | Beschreibung
1 | GND | Masse
2 | ENA | Schrittmotoren einschalten
3 | DIR | Richtung
4 | STEP | Schrittimpuls

PL204: Spindelmotor-Steuerung
Pin | Funktion | Beschreibung
1 | GND | Masse
2 | SPINDLE_PWM Pulsbreitenmoduliertes Signal für Spindel-Drehzahl
3 | SPINDLE_DIR | Drehrichtung Frässpindel (optional, z.B. für Umschaltrelais)
4 | VCC | +5V-Versorgungsspannung

Beide DIN-Steckleisten sowie deren Kontaktreihen a/b sind parallel geschaltet. Portleitungen sind im Unterschied zu den Steckverbindern nicht durch Widerstande geschützt! Beachten Sie, dass einige Leitungen mit einem Kondensator zur Erhöhung der Störsicherheit beschaltet sind.

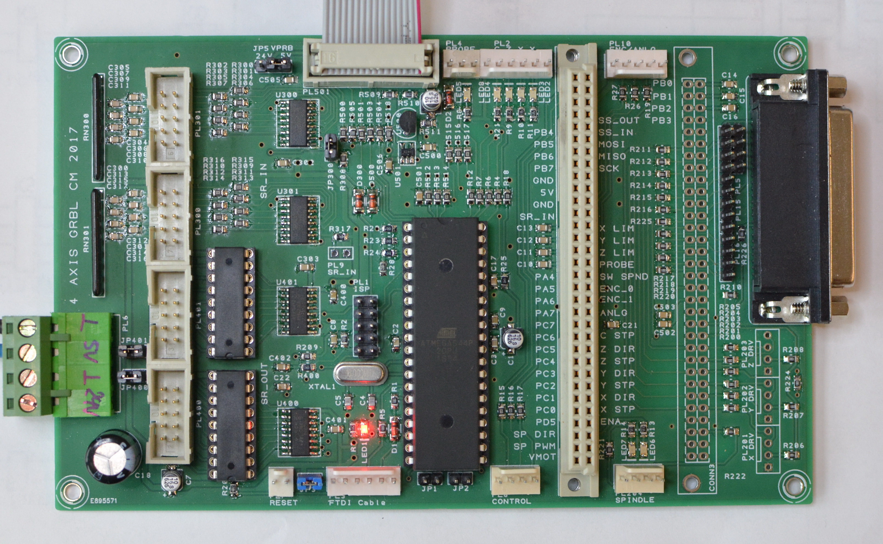
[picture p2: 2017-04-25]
maxyposi_pcb/platine_bestueckt.JPG

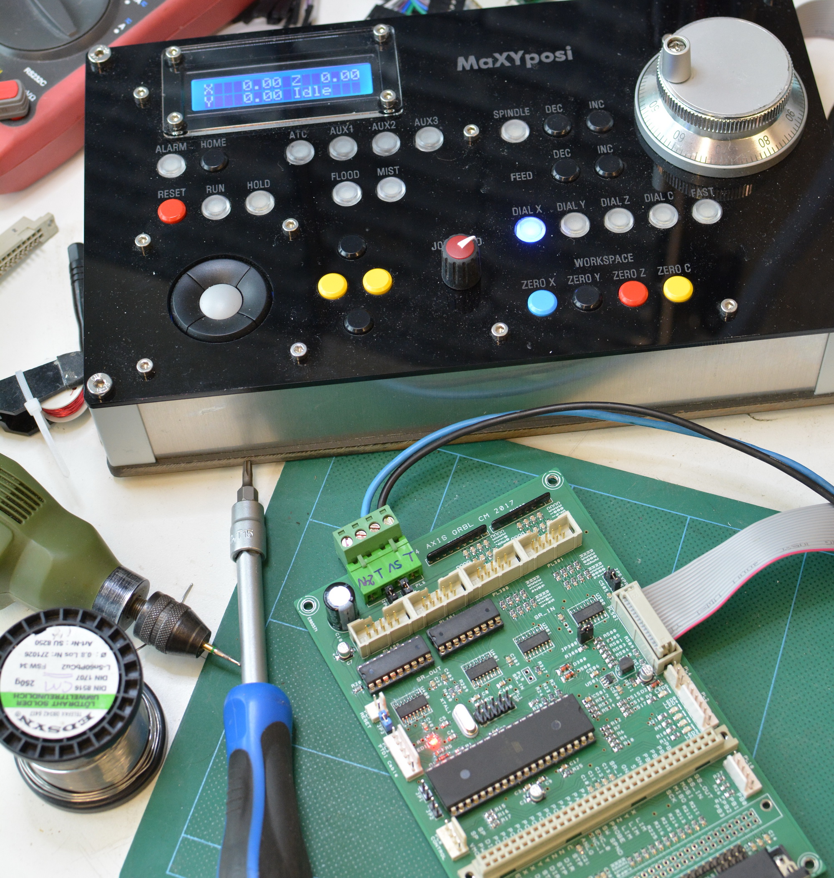
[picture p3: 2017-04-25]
maxyposi_pcb/platine_mit_panel.JPG

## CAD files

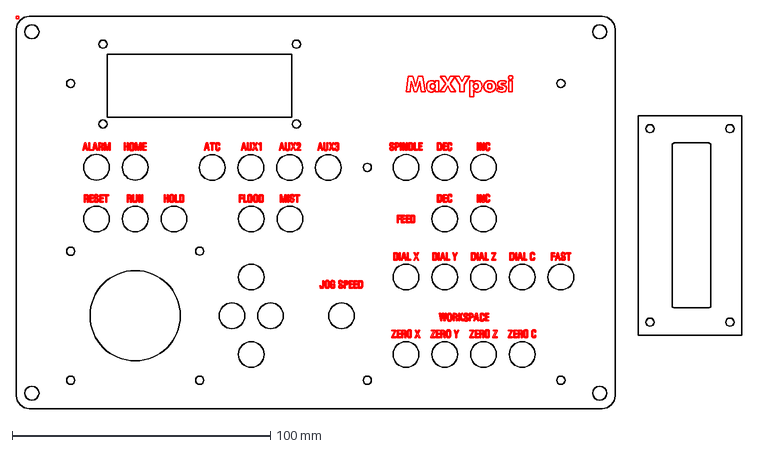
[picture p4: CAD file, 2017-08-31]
maxypulti_pcb/maxypulti_frontpl.dxf
281.0 x 152.0 mm

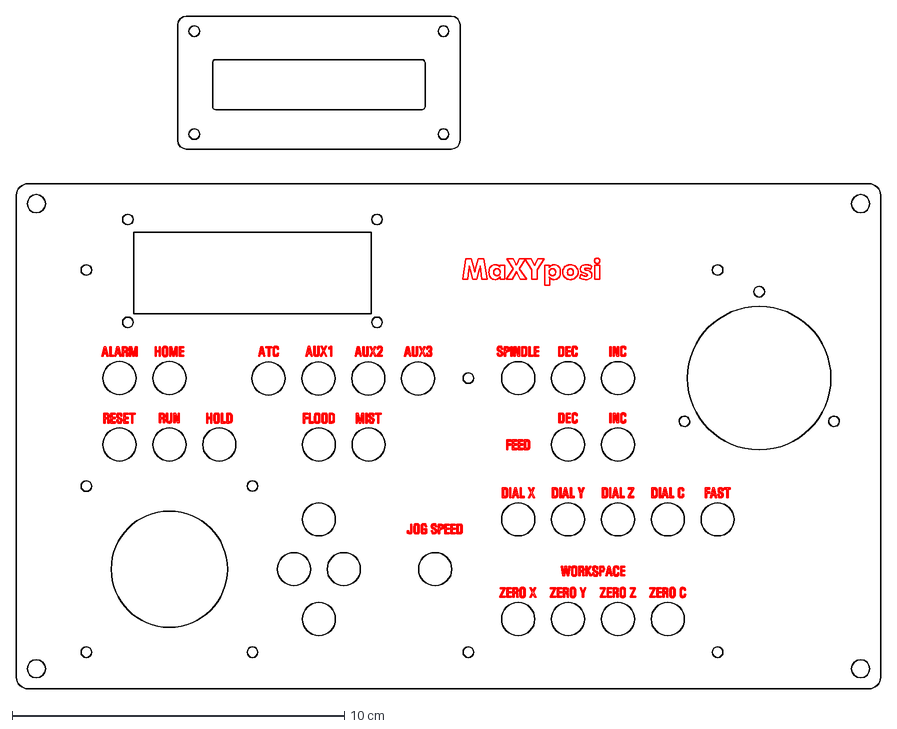
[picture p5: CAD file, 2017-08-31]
maxypulti_pcb/maxypulti_frontpl_dial.dxf
26.0 x 20.2 cm

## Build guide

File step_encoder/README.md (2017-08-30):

GitHub Logo

Maker Media GmbH und c't, Heise Zeitschriften Verlag

***

### MaXYposi-Schrittmotorsteuerung, Stückliste Step-Encoder

Einfache Schaltung, um einen alten Schrittmotor als Dreh-Encoder zu verwenden.

    Bauteil                               Anzahl Name/Bemerkung
    =============================================================================
    PSS 254/4G, Wire-To-Board 4-pol. RM2,54  6   PL1 PL2
    10µ 63V RM2.5                            2   C1, C2
    1N4148                                   4   D1..D4
    LED rot 3mm                              1   LED 1
    Widerstand 1 kOhm 1/4W                   2   R8, R11                    
    Widerstand 470 Ohm 1/4W                  3   R2, R7, R10                    
    Widerstand 47 Ohm 1/4W                   2   R5, R6                   
    LM 393 DIL                               1   U1                

Bitte denken Sie bei einer Bestellung auch an Zubehör wie Flachbandkabel, Steck-
und Pfostenverbinder.

Wer unbestückte Platinen fertigen (lassen) will, kann die Gerber- und 
Bohrdateien "stepenc_maxyposi_gerber.zip" herunterladen. Bitte beachten Sie: Das 
Layout unterliegt unserem Copyright und darf **nur für private Zwecke** verwendet 
werden. Für eine kommerzielle Nutzung [kontaktieren Sie bitte die 
Redaktion](https://www.heise.de/make/kontakt/).

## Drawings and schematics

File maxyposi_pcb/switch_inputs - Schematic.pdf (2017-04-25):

# GRBL-Controller 2.1 Inputs

# C. Meyer 02/2017

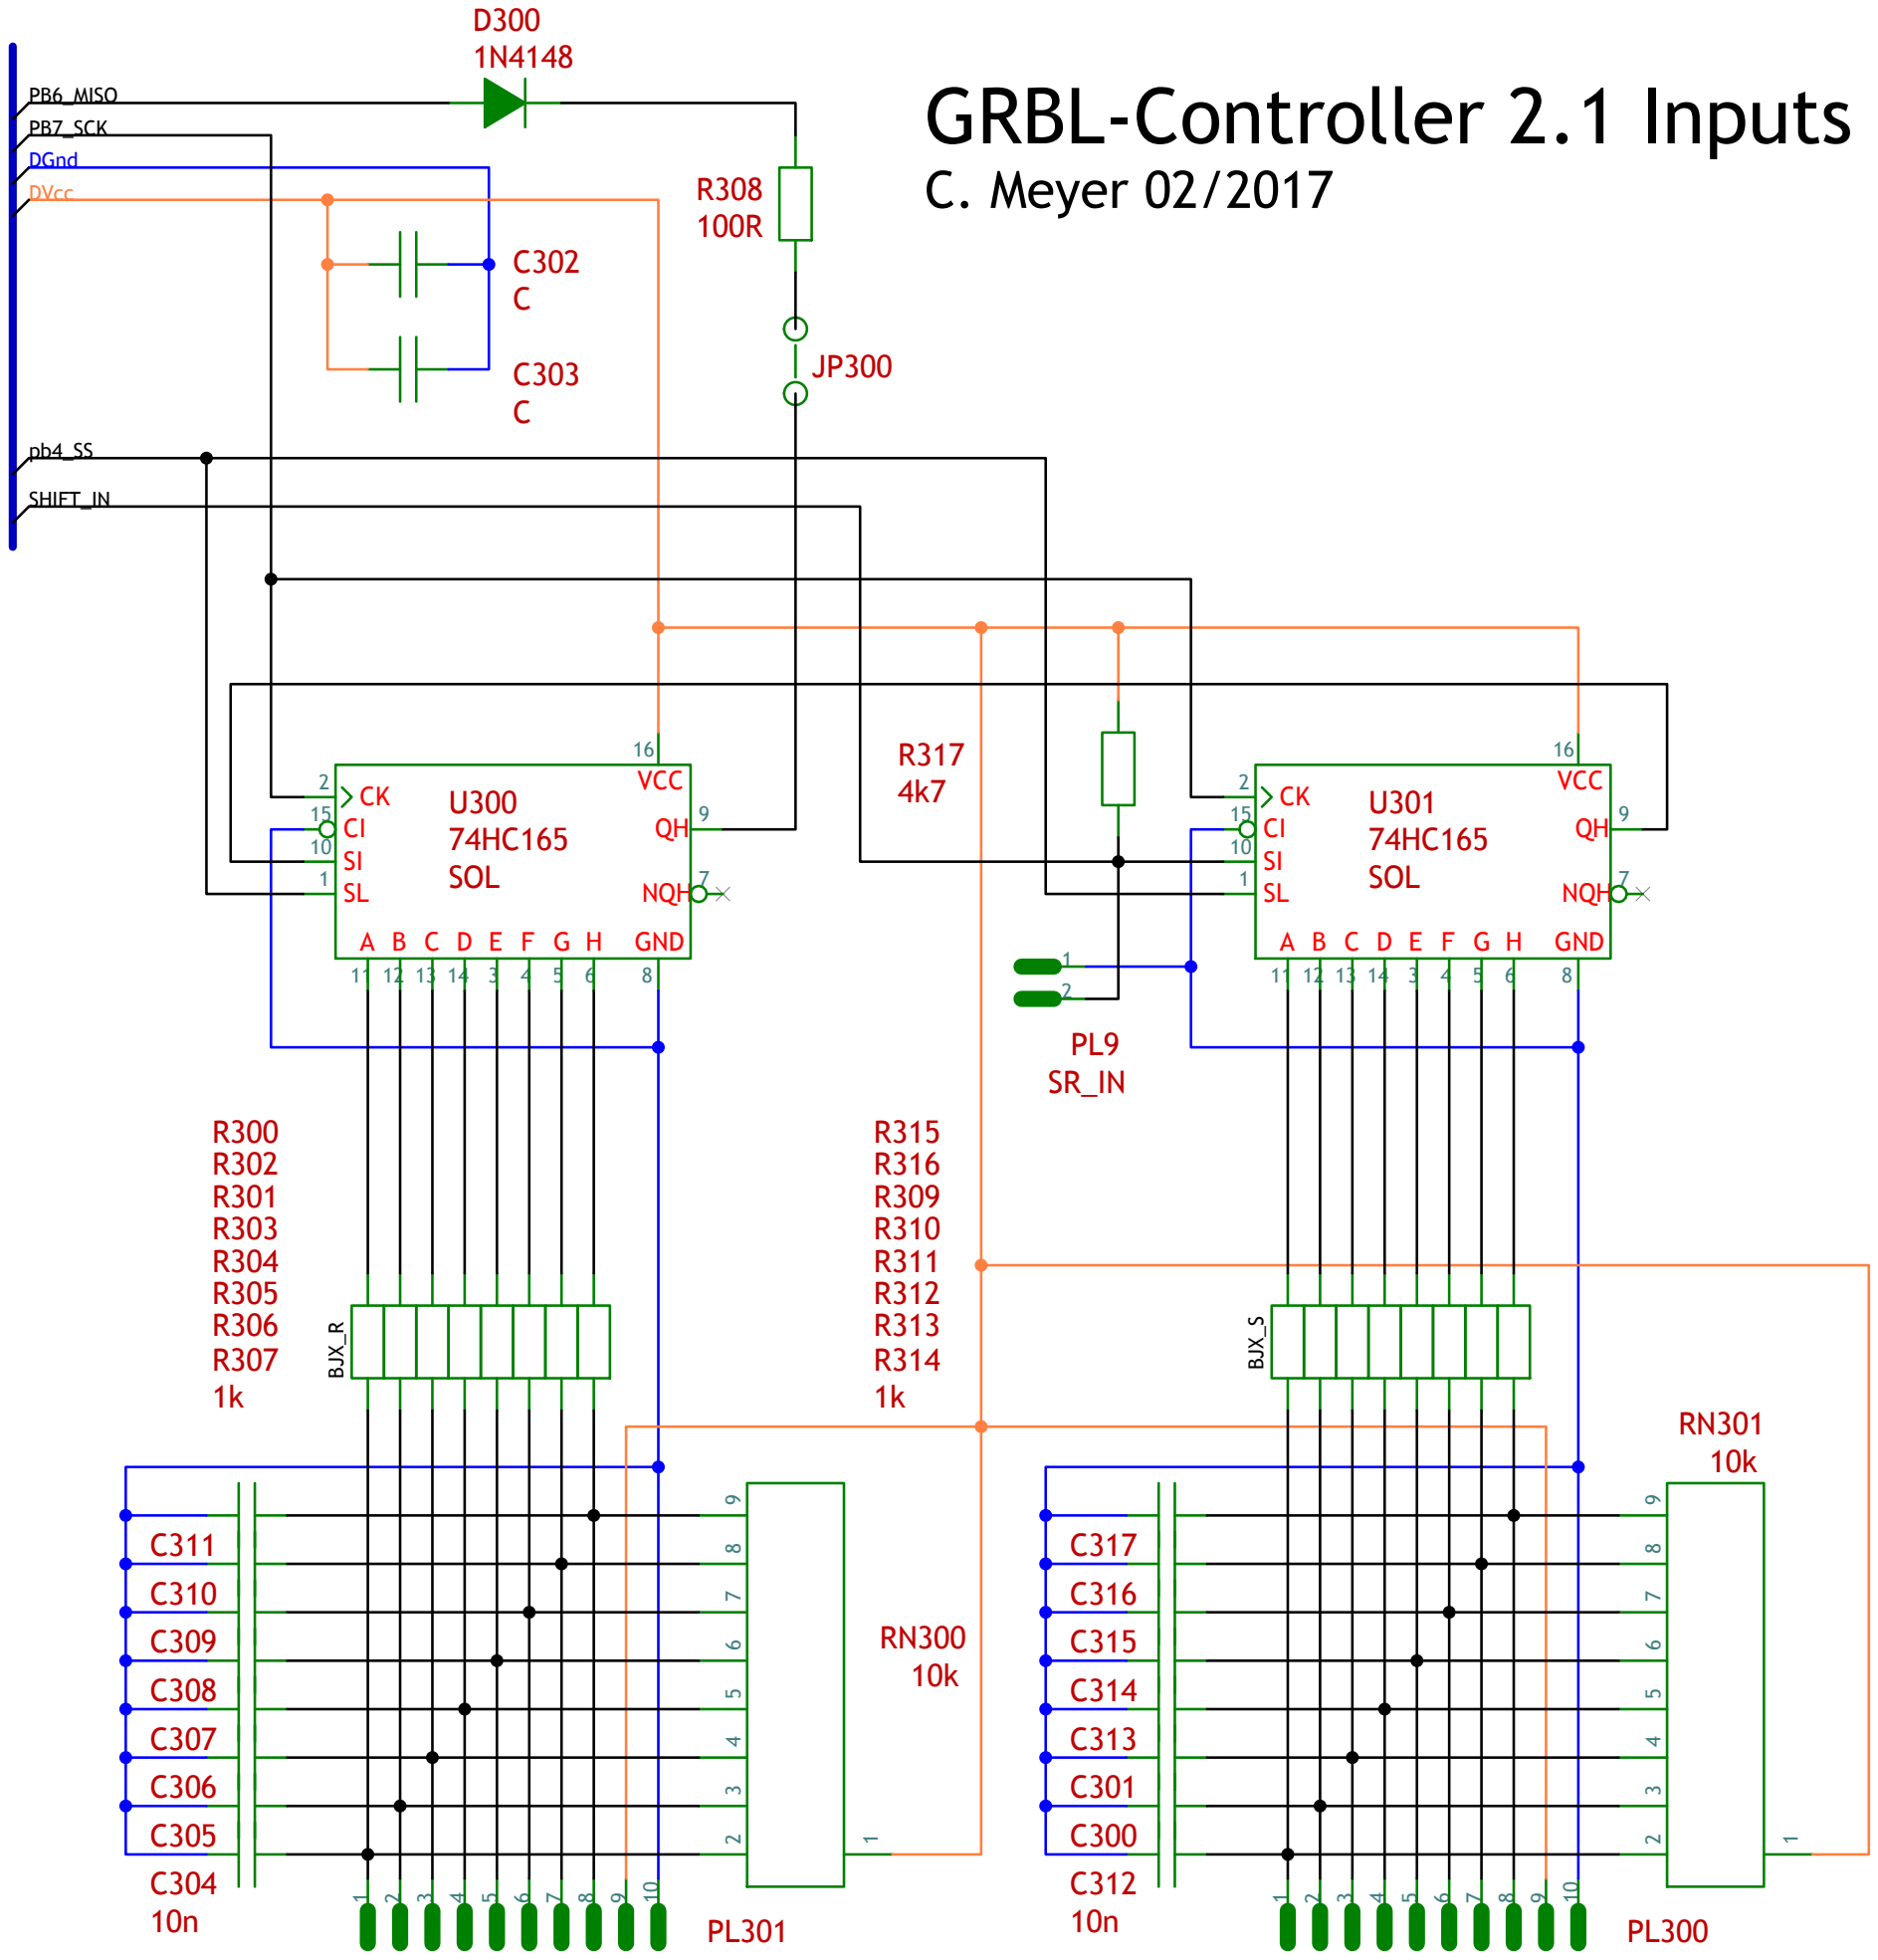
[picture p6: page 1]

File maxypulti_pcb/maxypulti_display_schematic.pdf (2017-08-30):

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

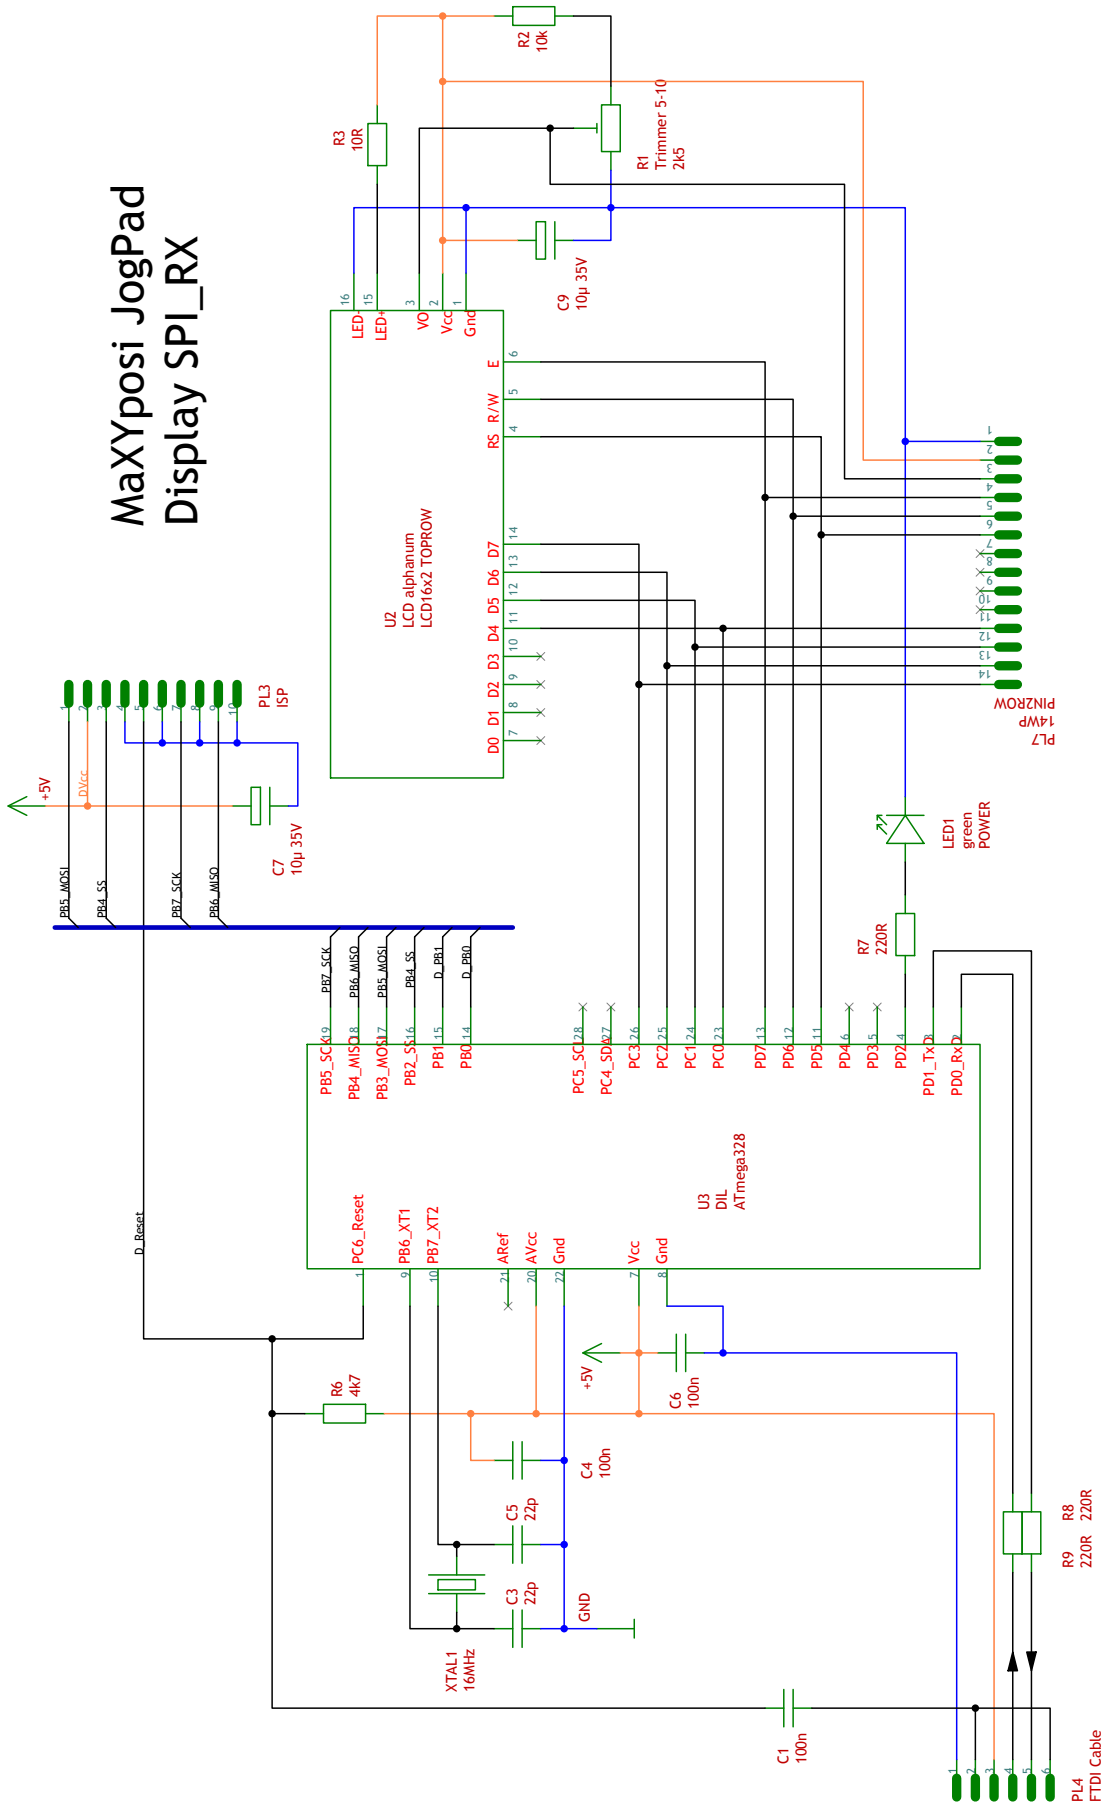
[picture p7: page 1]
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

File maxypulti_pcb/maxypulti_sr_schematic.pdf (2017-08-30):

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

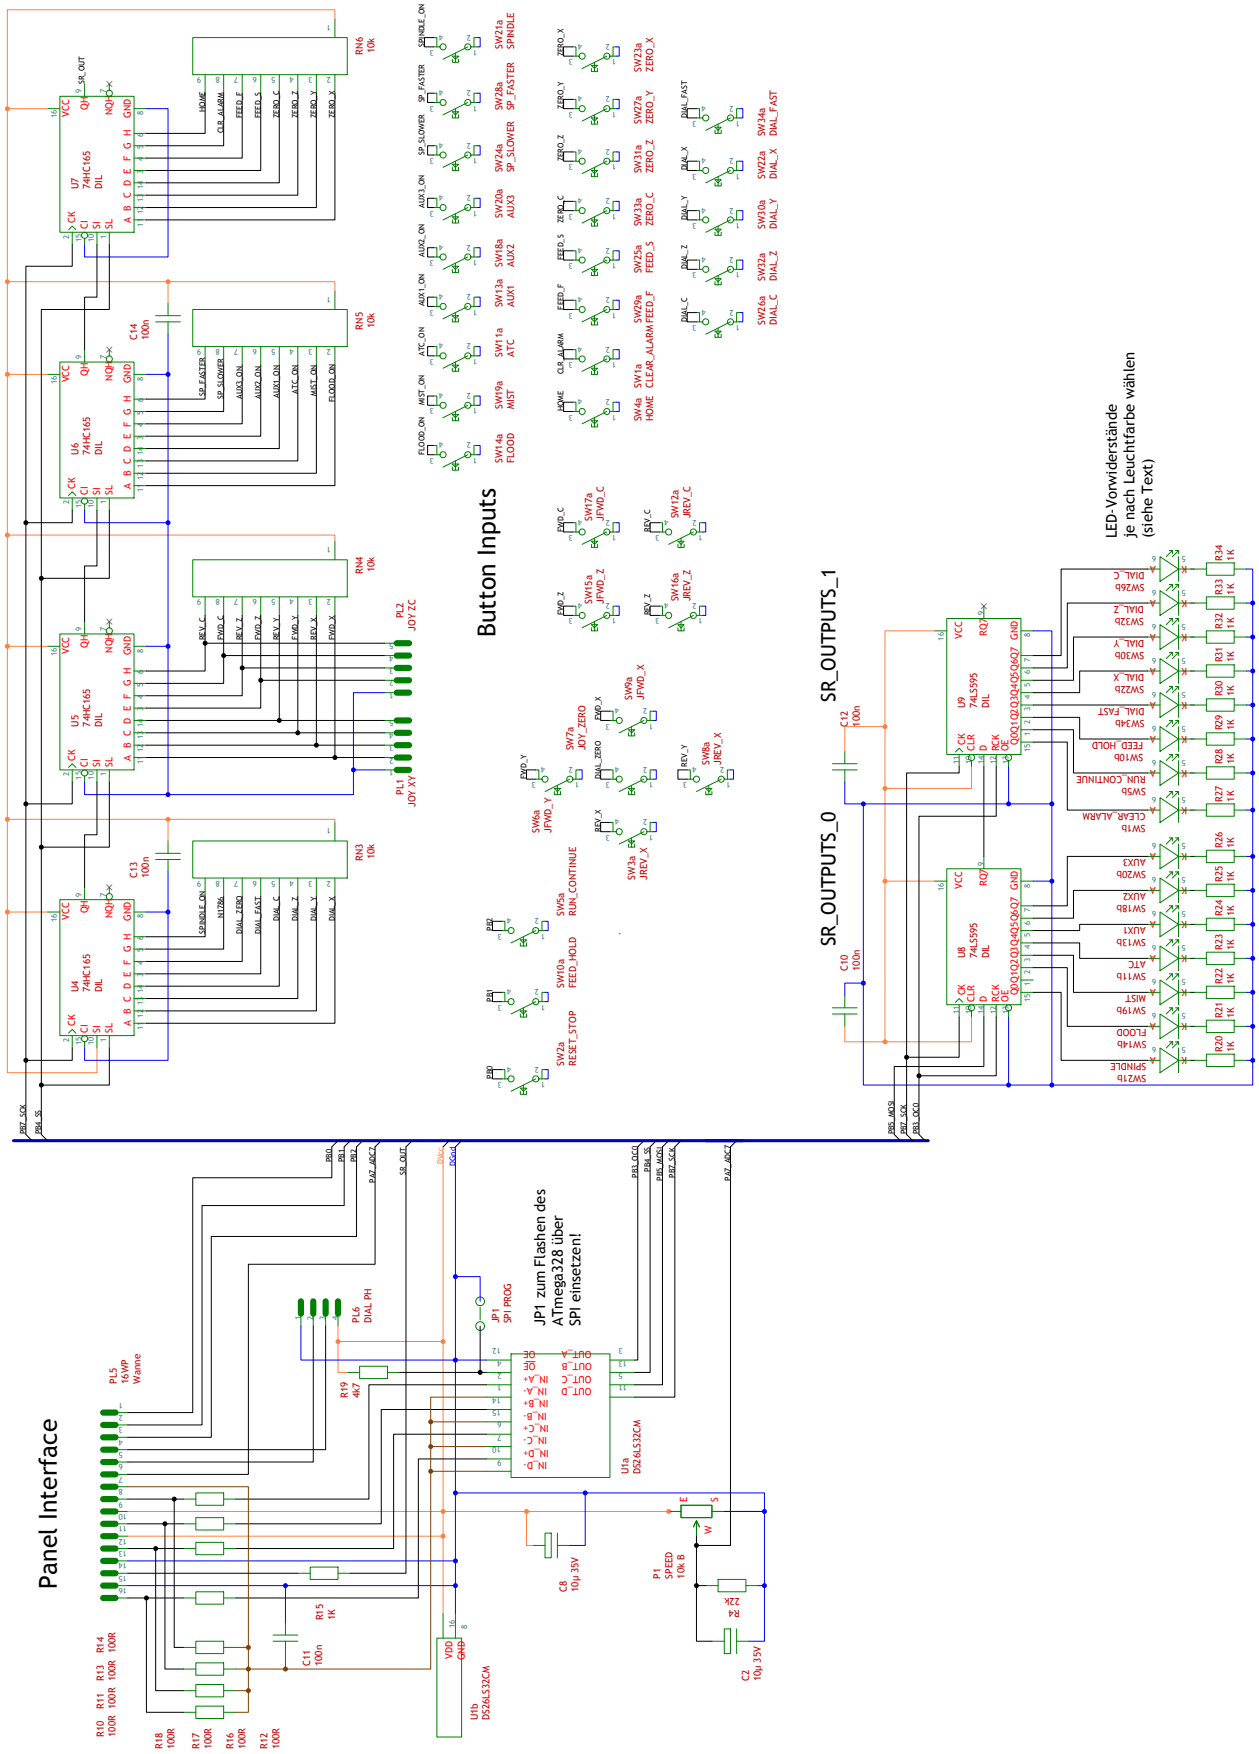
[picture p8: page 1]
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

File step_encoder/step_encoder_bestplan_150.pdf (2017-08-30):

C1

D1

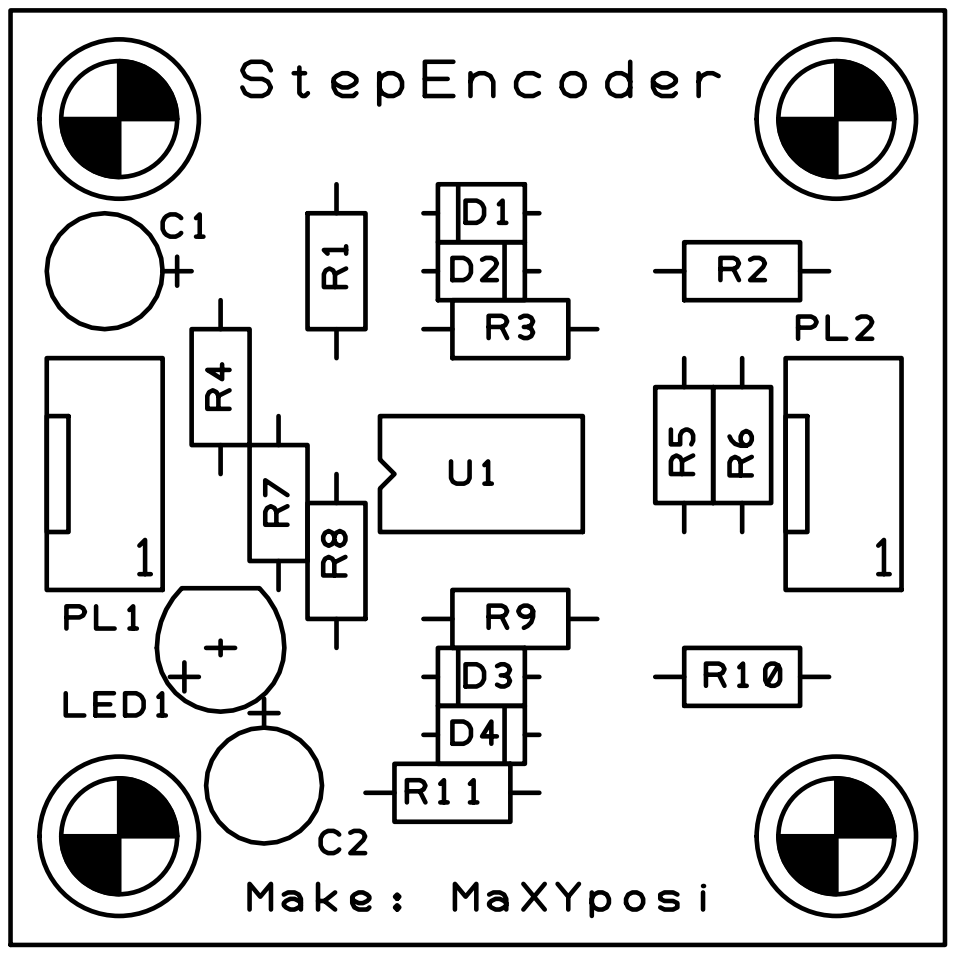
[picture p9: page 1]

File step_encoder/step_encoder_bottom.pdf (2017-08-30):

C1

D1

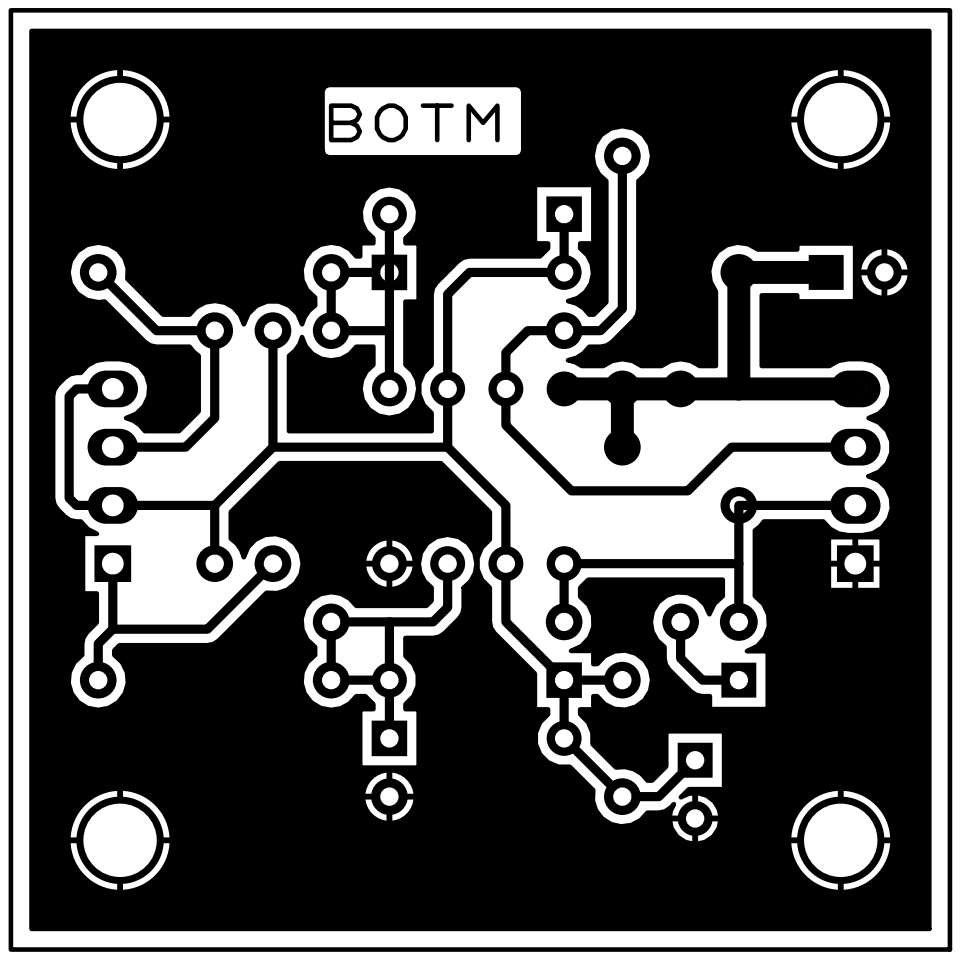
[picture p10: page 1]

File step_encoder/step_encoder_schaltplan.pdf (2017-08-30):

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

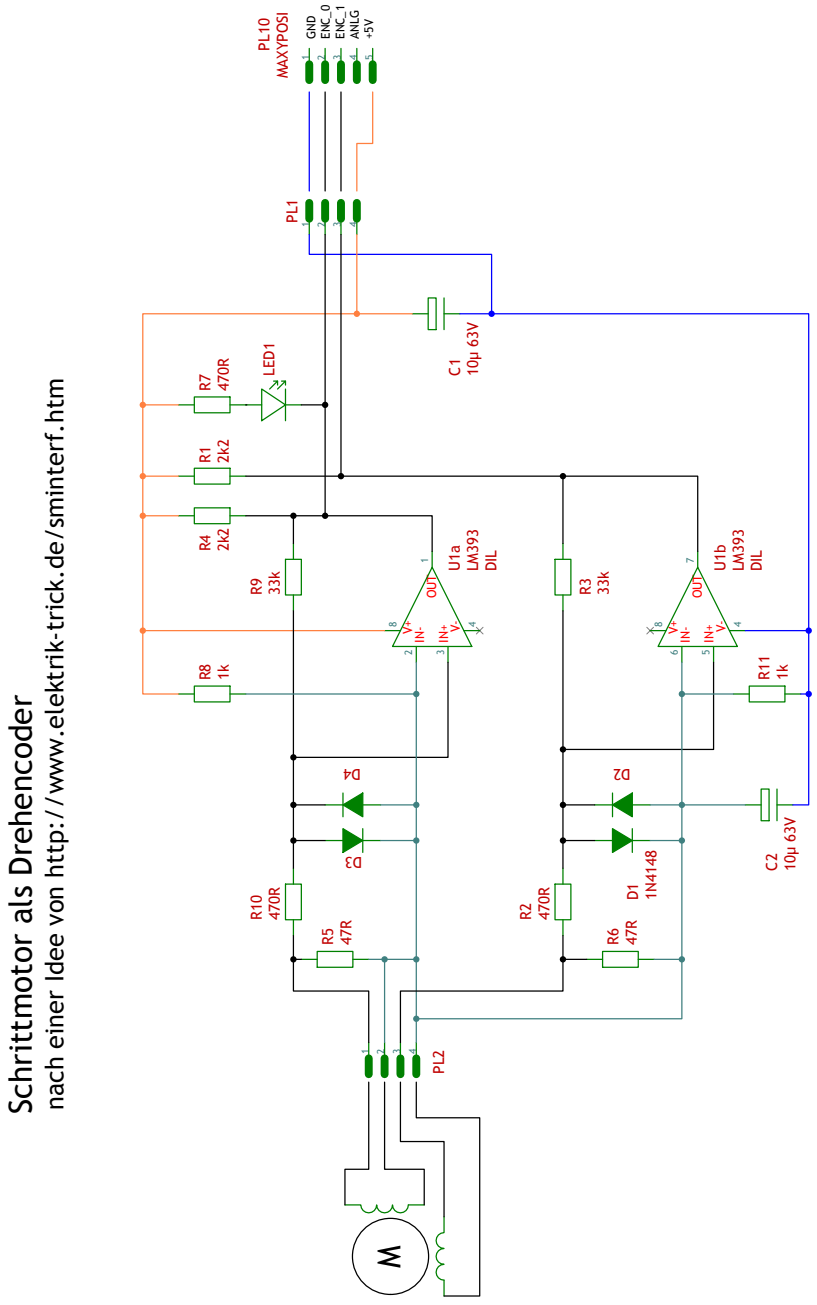
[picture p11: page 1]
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

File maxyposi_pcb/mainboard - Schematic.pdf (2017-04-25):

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

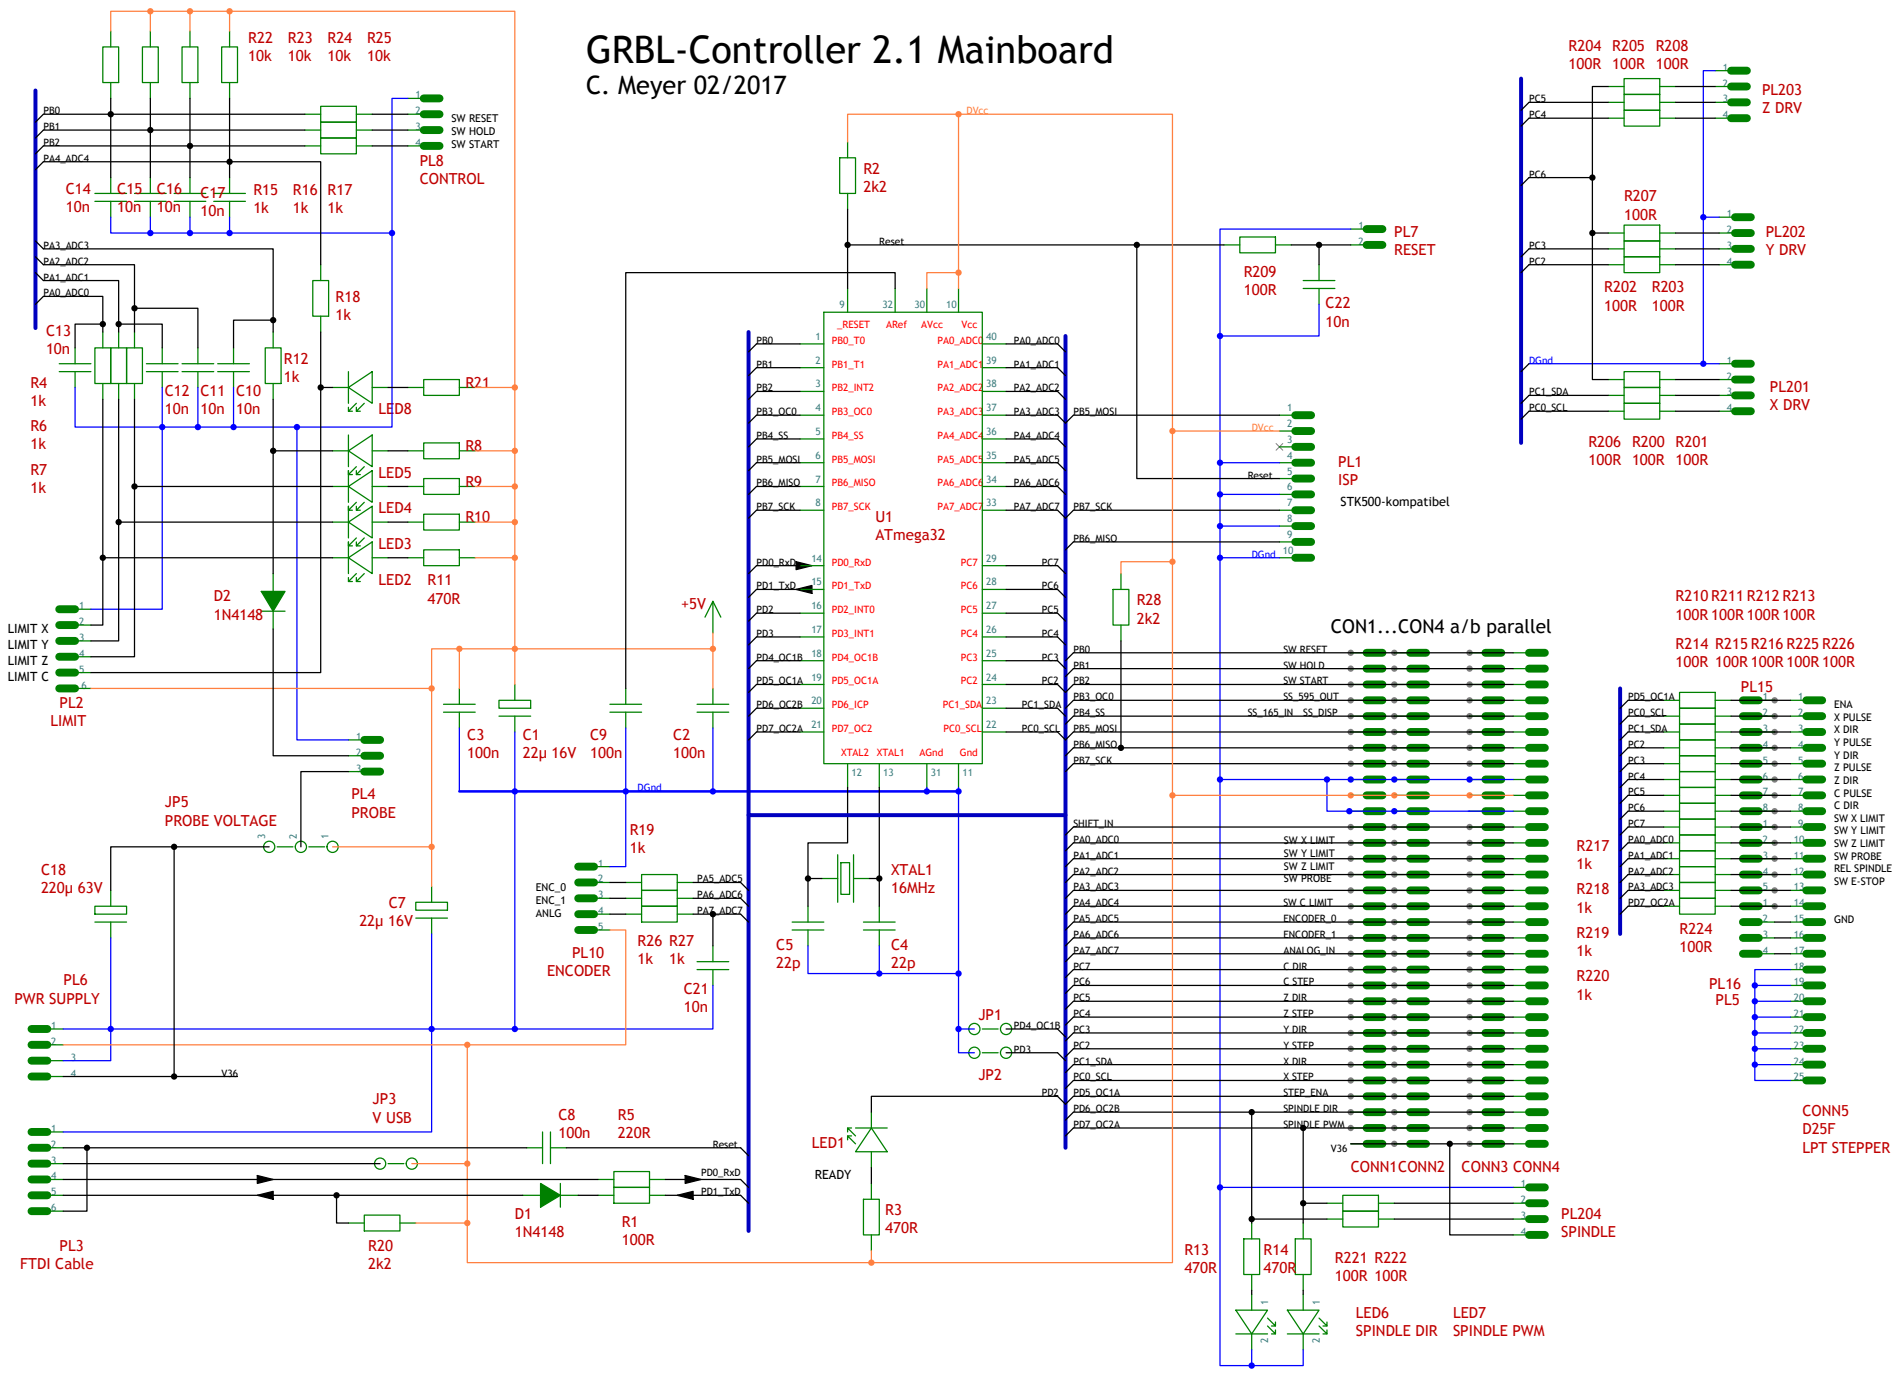
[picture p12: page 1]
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

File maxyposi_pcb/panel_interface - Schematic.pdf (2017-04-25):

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

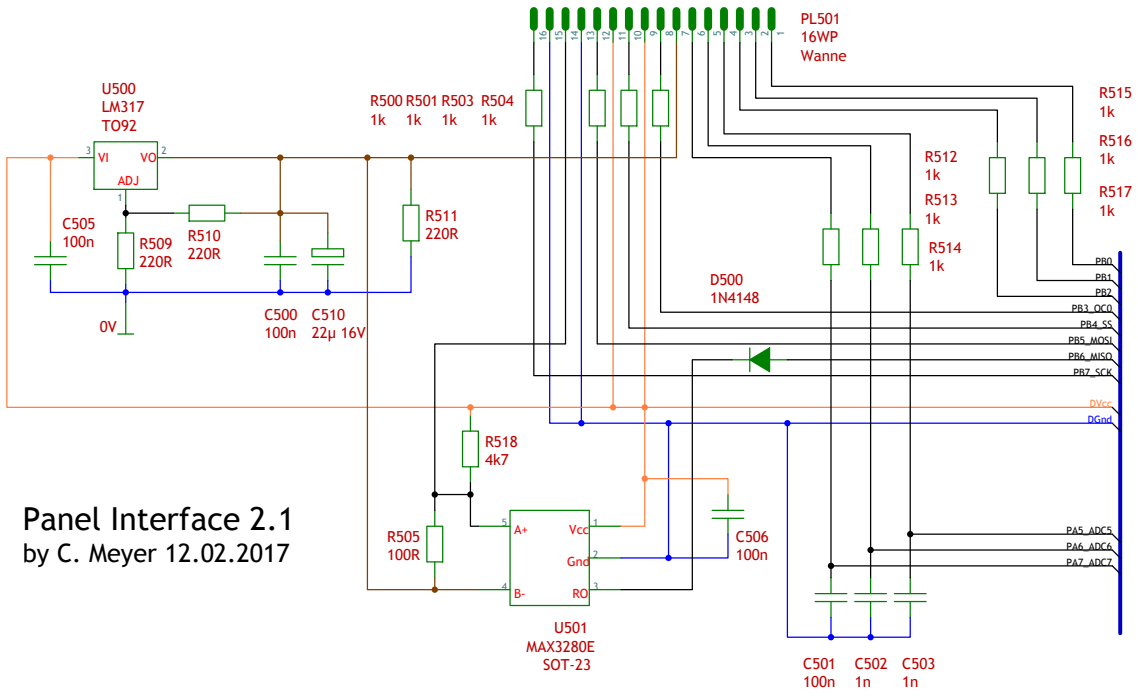
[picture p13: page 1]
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

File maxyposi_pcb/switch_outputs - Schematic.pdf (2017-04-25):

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

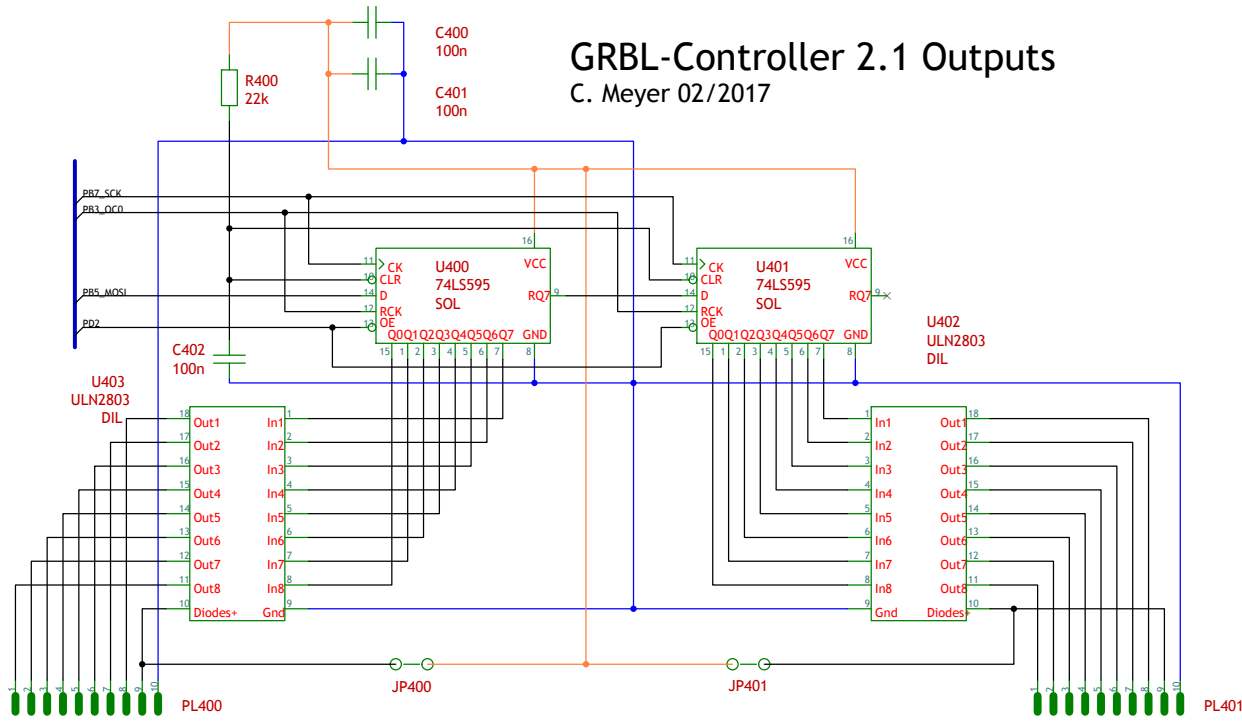
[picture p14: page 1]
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

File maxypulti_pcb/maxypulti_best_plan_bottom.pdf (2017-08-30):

C9

R2

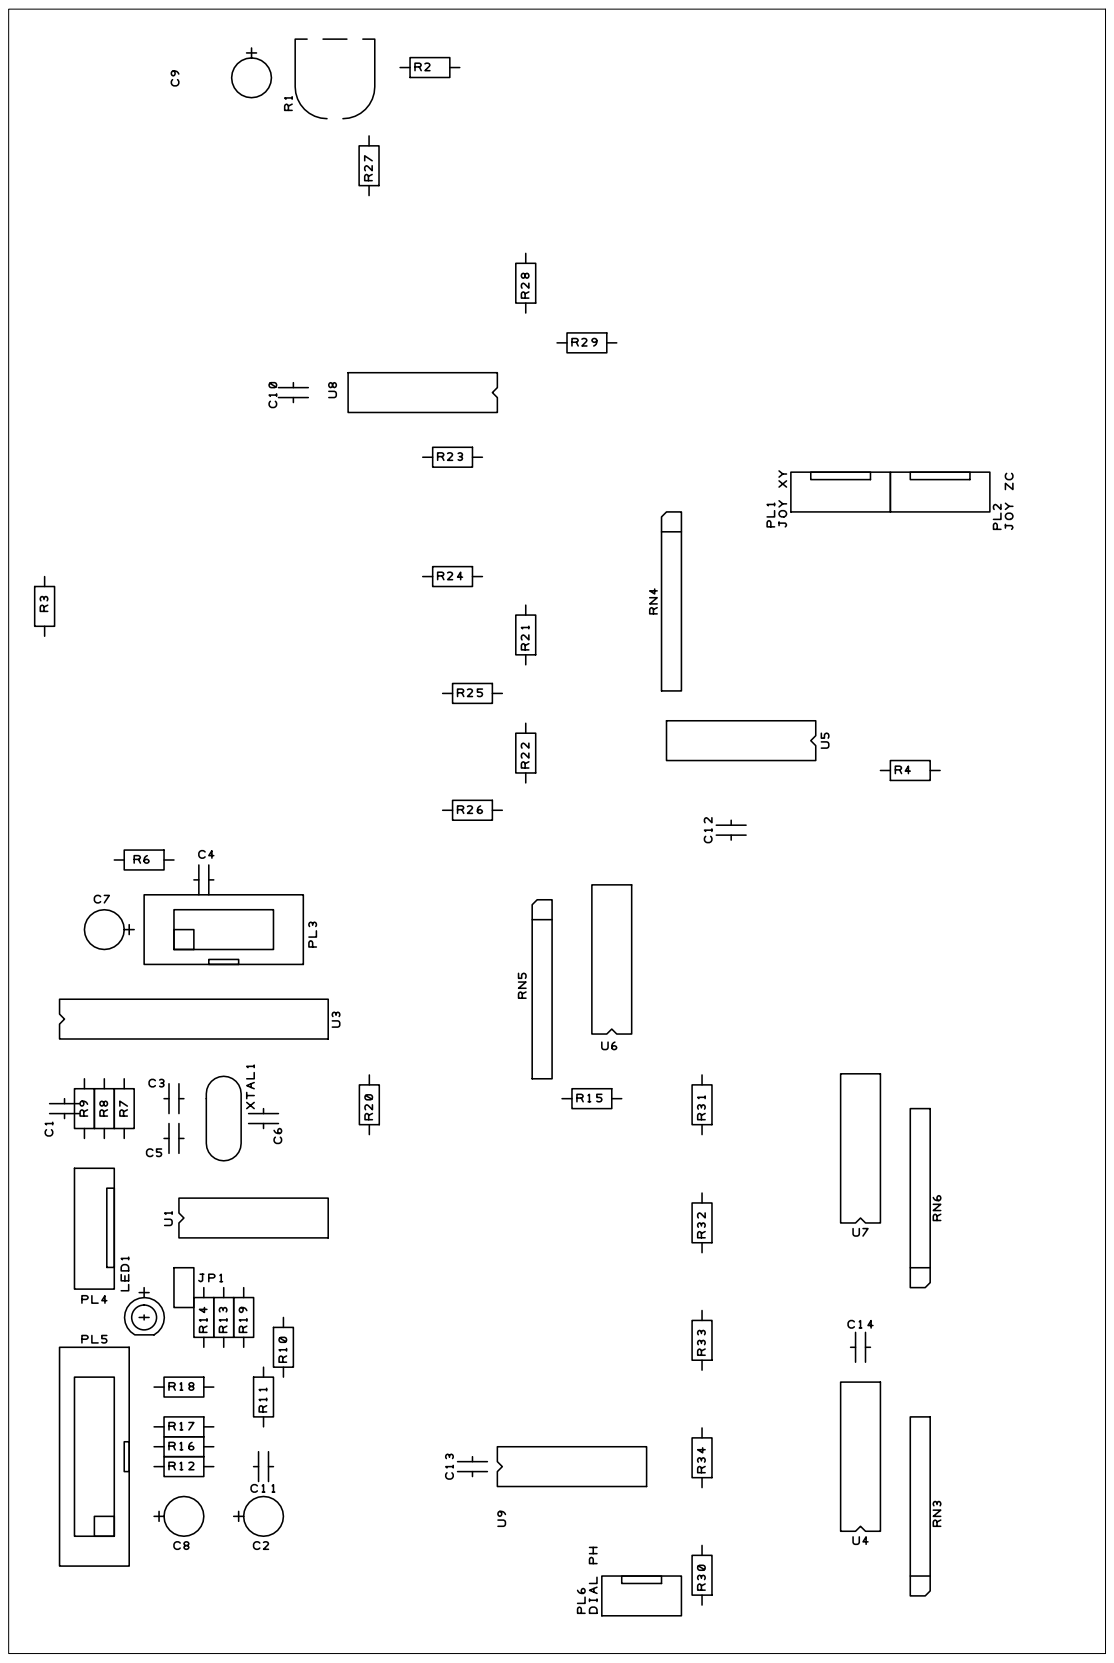
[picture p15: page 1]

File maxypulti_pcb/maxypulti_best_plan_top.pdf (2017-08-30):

Mt8

Mt9

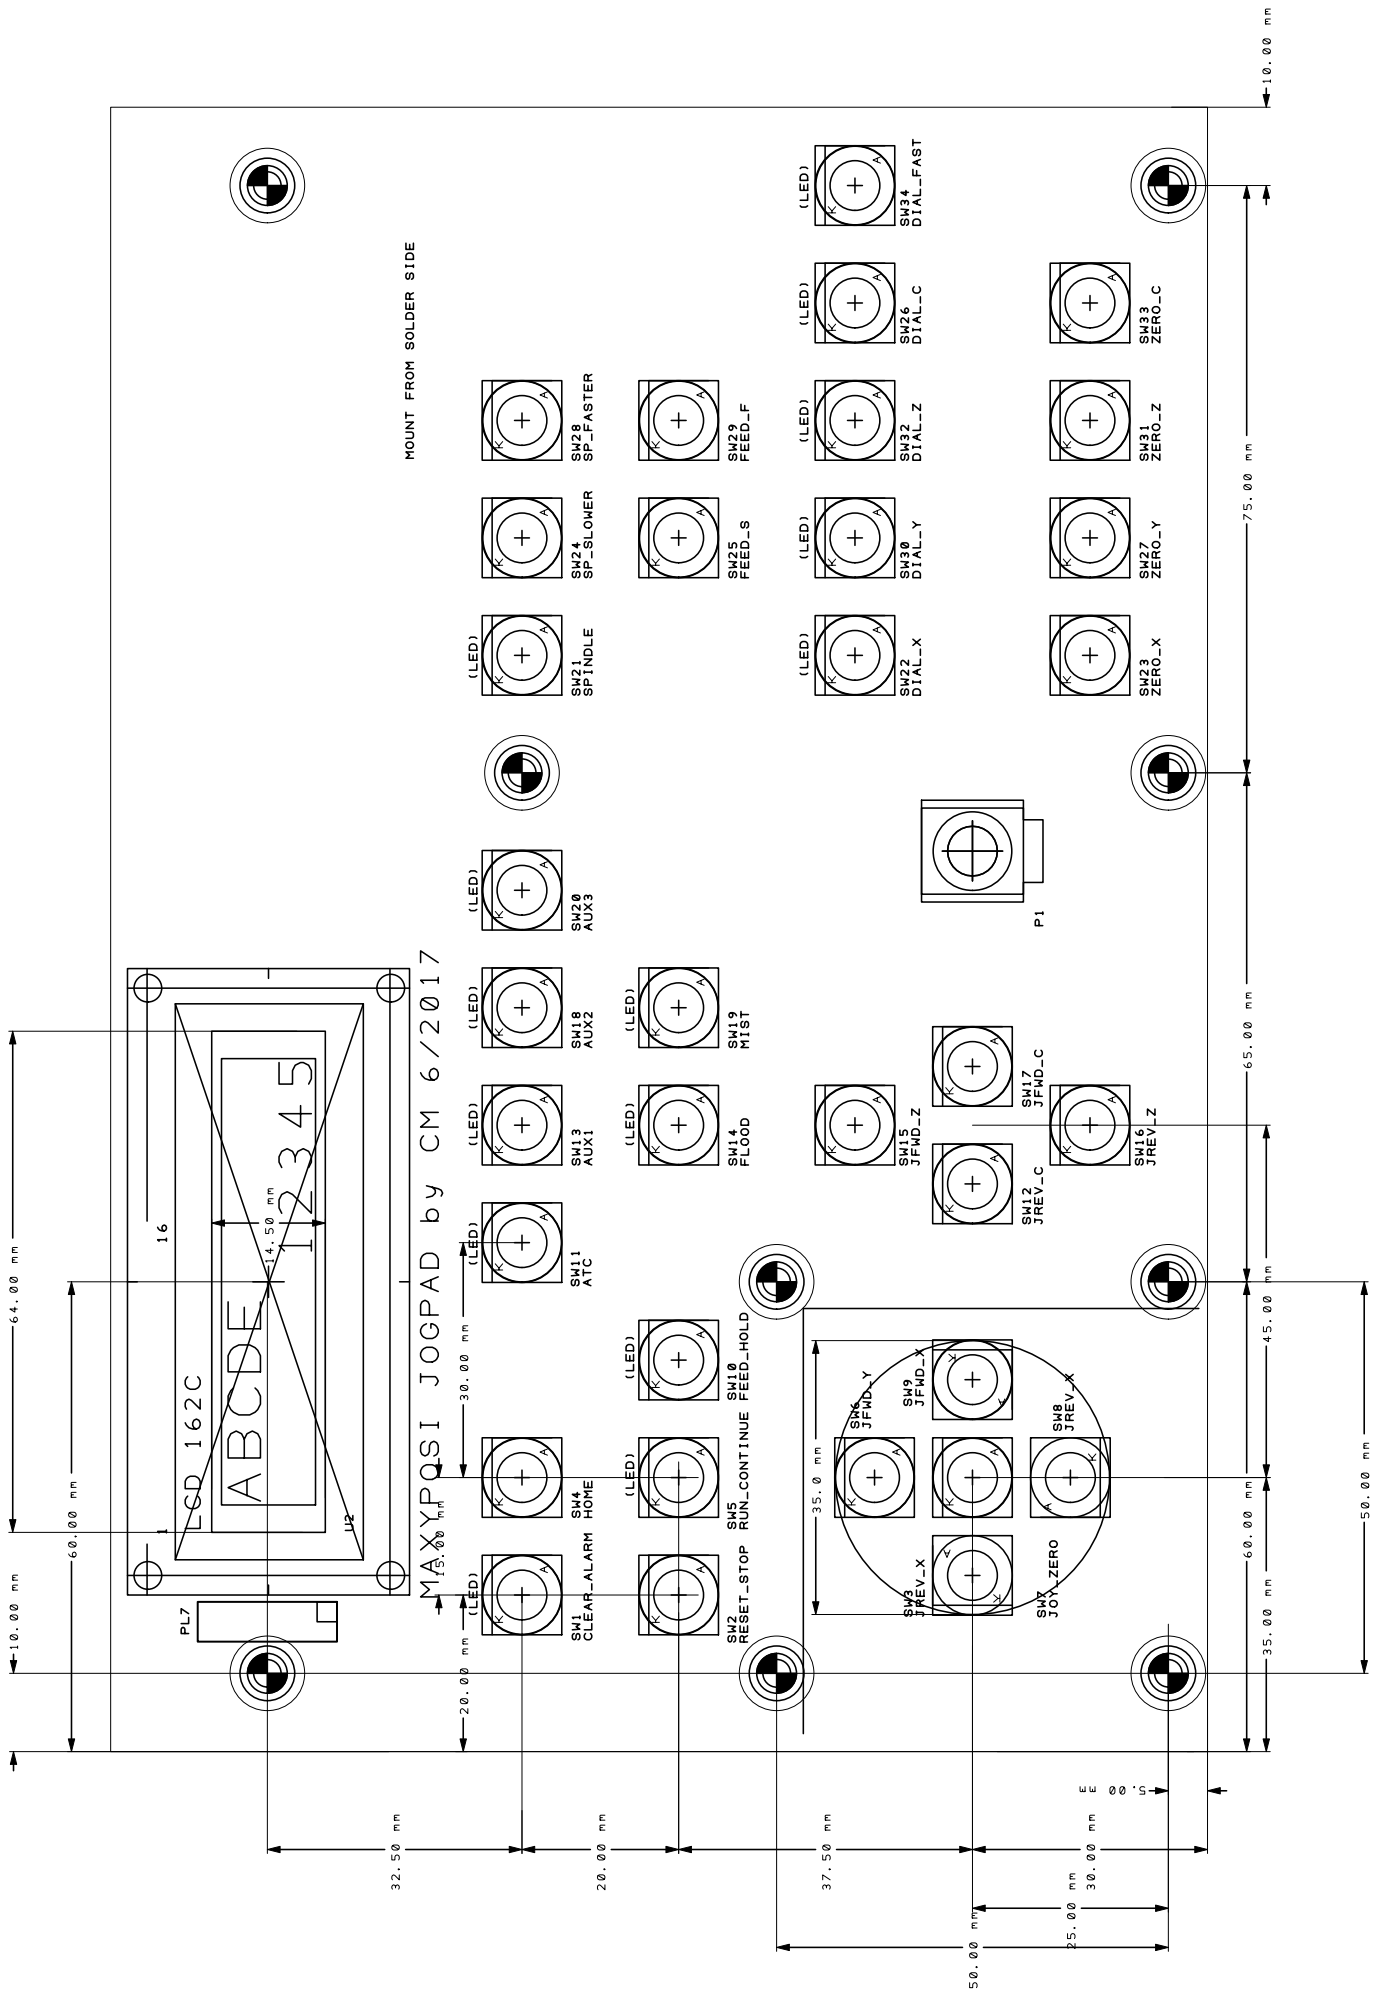
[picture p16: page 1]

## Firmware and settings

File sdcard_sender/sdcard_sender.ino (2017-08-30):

/*
  SD card file dump

 This example shows how to read a file from the SD card using the
 SD library and send it over the serial port.

 The circuit:
 * SD card attached to SPI bus as follows:
 ** MOSI - pin 11
 ** MISO - pin 12
 ** CLK - pin 13
 ** CS - pin 4 (for MKRZero SD: SDCARD_SS_PIN)

 created  22 December 2010
 by Limor Fried
 modified 9 Apr 2012
 by Tom Igoe

 This example code is in the public domain.

 */

#include <SPI.h>
#include <SD.h>

const int chipSelect = 8;
String inputString = "";         // a string to hold incoming data
boolean ready_to_run = false;

void setup() {
  inputString.reserve(200);
  // Open serial communications and wait for port to open:
  Serial.begin(115200);
  while (!Serial) {
    ; // wait for serial port to connect. Needed for native USB port only
  }
}

void serial_readln(){
  boolean got_cr = false;
  inputString = "";
	do {
	  while (Serial.available()) {
	    char inChar = (char)Serial.read();
	    inputString += inChar;
	    if (inChar == 13) {
	      got_cr = true;
	    }
	  }
	}	while (!got_cr);
}

void file_send(){
  // open the file. note that only one file can be open at a time,
  // so you have to close this one before opening another.
  // SerialEvent will not work while active!
  // see if the card is present and can be initialized:
  if (!SD.begin(chipSelect)) {
    Serial.println("(SD Card failed or not present)");
  }
//  Serial.println("(SD card initialized)");

  File dataFile = SD.open("gcode.txt");
  char c;
  // if the file is available, read from it:
  if (dataFile) {
    while (dataFile.available()) {
      c = dataFile.read();
      if (c >= 32) Serial.write(c);
      if (c==13) {
  			while (Serial.available()) Serial.read();
      	Serial.write(c);
        serial_readln();
        delay(25);
			  if (inputString.indexOf("Pn:R") >= 0) break;
      }
    }
    dataFile.close();
  }
  // if the file isn't open, pop up an error:
  else {
    Serial.println("(error opening gcode.txt)");
  }
  delay(500);
}

void loop() {

  char c;
  while (Serial.available()) Serial.read();
  Serial.write('?');
  serial_readln();
  if (inputString.indexOf("Idle") >= 0)  ready_to_run = true;
  if (inputString.indexOf("Run") >= 0)   ready_to_run = false;
  if (inputString.indexOf("Hold") >= 0)  ready_to_run = false;
  if (inputString.indexOf("Alarm") >= 0) ready_to_run = false;
  if (ready_to_run && (inputString.indexOf("Pn:S")) >= 0){
    file_send();
  }
  delay(100);
}

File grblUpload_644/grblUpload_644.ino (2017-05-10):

/***************************************************************************

Dieser Sketch kompiliert GRBL-644 und lädt es auf die MaXYposi-Platine. Bitte 
richten Sie die Arduino-IDE folgendermaßen ein:

- Verschieben Sie das Verzeichnis "grblUpload_644" vom Github-Download in Ihren "Arduino"-Sketch-Ordner.
- Verschieben Sie das Verzeichnis "hardware" vom Github-Download in Ihren "Arduino"-Sketch-Ordner.
- Verschieben Sie das Verzeichnis "libraries\grbl_644" vom Github-Download nach "Arduino\libraries\grbl_644".
- Öffnen Sie den Sketch "..\Arduino\grblUpload_644\grblUpload_644.ino"
- Wählen Sie im Menü "Werkzeuge:Board" den Eintrag "MaXYposi".
- Wählen Sie im Menü "Werkzeuge:Prozessor" den Eintrag "ATmega644A" oder "ATmega644P", je nachdem, welche Variante Sie verwenden.

Sie können nun GRBL mit der Arduino-IDE kompilieren und auch auf das Board 
hochladen; die mit der Platine gelieferten prozessoren sind bereits mit einem 
Sanguino-Optiboot-kompatiblen Bootloader ausgestattet.

****************************************************************************

This sketch compiles and uploads Grbl_644 to your 644p-based MaXYposi Board!

GrblUpload changed by -cm to explicitely use grbl_644 library

To use:
- Copy enclosed "hardware" directory into your Arduino directory.
- Copy entire "grbl_644" directory into "libraries" inside your Arduino directory.
- Select "MaXYiposi" board.
- Check if your CPU is ATmega644A or ATmega644P. Select CPU menu accordingly.
- FTDI device's Serial Port in the Tools drop-down menu.

- Then just click 'Upload'. That's it!

For advanced users:

  If you'd like to see what else Grbl can do, there are some additional
  options for customization and features you can enable or disable. 
  Navigate your file system to where the Arduino IDE has stored the Grbl 
  source code files, open the 'config.h' file in your favorite text 
  editor. Inside are dozens of feature descriptions and #defines. Simply
  comment or uncomment the #defines or alter their assigned values, save
  your changes, and then click 'Upload' here. 

Copyright (c) 2015 Sungeun K. Jeon
Released under the MIT-license. See license.txt for details.
***************************************************************************/

#include <grbl_644.h>

// Do not alter this file!

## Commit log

2017-03-03 jogpad handling
    [config.h, cpu_map.h, defaults.h]
2017-03-03 grbl for ATmega644
2017-03-03 4th axis support, BETA
    [config.h, cpu_map.h, defaults.h]
2017-03-03 4th axis support
    [alarm_codes_en_US.csv, build_option_codes_en_US.csv, config.h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]
2017-03-04 First time 4 axis working.
    [config.h, cpu_map.h, defaults.h]
2017-03-04 new git
    [config.h, cpu_map.h, defaults.h]
2017-03-10 homing of C axis
2017-03-10 homing c axis
2017-04-24 Board Info
2017-04-25 BOM added
2017-04-25 added schematics
2017-06-20 1.1f3, Laser Mode fix
2017-08-31 Update Frontplatten
    [maxypulti_frontpl.dxf, maxypulti_frontpl_dial.dxf]
2017-09-04 drill changes
2018-02-23 Hinweise zu GRBL
2018-02-23 1.1f5 bugfix
    [pinout_mainboard.xls]
2018-04-14 Use (limits_get_state())
    to identify limit switches
2018-04-14 Remove add. brackets
2018-04-14 Initialize joy_axis to 0
    Fixes warning about it being uninitialized. No idea if 0 is correct, but it is probably the X-axis, so that should be fine...
